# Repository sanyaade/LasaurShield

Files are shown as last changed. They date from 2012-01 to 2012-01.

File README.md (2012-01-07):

The LasaurShield is a custom PCB for the [Lasersaur project](http://lasersaur.com). It's an [Arduino](http://arduino.cc/) [shield](http://arduino.cc/en/Main/ArduinoShields) that connects laser, stepper, stepper driver, stepper power, limit switches, door sensor, water chiller sensor, emergency stop sensor, and Arduino. Starting with v11.10 the core safety functions are also hardwired on the board.

The LasaurShield is designed around the SparkFun Eagle Library, their design and CAM job rules. Check out the [SparkFun Tutorial](http://www.sparkfun.com/tutorials/108) if you are new to this. If you are interesting doing your own production run check out [this tutorial](http://www.sparkfun.com/tutorials/109).

The following Eagle library and design files are being used:

- cam/sparkfun-gerb274x.cam
- dru/LasaurShield.dru
- lbr/[SparkFun.lbr]
- lbr/con-phoenix-254.lbr (comes with Eagle)
- lbr/con-phoenix-508.lbr (comes with Eagle)
- lbr/con-weidmueller-sl35.lbr (comes with Eagle)

**DISCLAIMER:** Please be aware that operating a DIY laser cutter can be dangerous and requires full awareness of the risks involved. You build the machine and you will have to make sure it is safe. The instructions of the Lasersaur project and related software come without any warranty or guarantees whatsoever. All information is provided as-is and without claims to mechanical or electrical fitness, safety, or usefulness. You are fully responsible for doing your own evaluations and making sure your system does not burn, blind, or electrocute people.

Some Notes about Using Eagle
=============================

Eagle is quite powerful but also awkward to use. It's easy to forget how to command the UI.

When designing the schematic
------------------------------
- import parts libraries, Library->Use
- some parts like the NAND gates require you to press the "Invoke" button and place power and ground. Don't ask me why.
- Once the schematic is done, run the electrical checks Tools->Erc

When laying out the board
--------------------------
- load design rules, Tools->Drc  (dru/LasaurShield.dru)
- place components, move/rotate to optimize the ratsnest
- color layers as needed, View->Display/hide layers
  - 121 _tsilk  ... is top silkscreen
  - 122 _bsilk  ... is bottom silkscreen
- run autoroute, 
  - The power of the autorouter is that it can be used incrementally. Some wires can be drawn manually and the autorouter can finish the rest. 
  - Another great approach is to draw some wires roughly (e.g. on one side of the board) then autoroute, rip the manual wires and autoroute again. This way the autorouter follows the general idea but draws the wires nicely.
- if the autorouter should use different trace widths this can be accomplished by defining net classes with different widths, Edit->Net classes
  - air wires of the ratsnest (it actually applies to the entire signal) can then be assigned to the various net classes

When creating the CAM Job (gerber files)
-----------------------------------------
- run final design rule check, Tools->Drc
- Open the CAM Processor, File->Cam Processor
- Open the CAM rule file, File->Open->Job   (cam/sparkfun-gerb274x.cam)
- Press "Process Job"
- At this point Eagle creates a bunch of files in the same directory as the board file. 
  - Top Copper (GTL)
  - Top Soldermask (GTS)
  - Top Silkscreen (GTO)
  - Bottom Copper (GBL)
  - Bottom Soldermask (GBS)
  - Bottom Silkscreen (GBO)
  - Drill File (TXT)
  - Drill Summary (dri)
- before sending these to a manufacturing house check them with [Viewplot](http://www.viewplot.com/) or by uploading a zip to [circuitpeople.com](http://circuitpeople.com/).

Parts List for v11.11 Upgrade
==============================

2   resistor 10 KOhm    271-10K-RC    (making it a total of 7x)
1   e-stop button 24mm    642-A01ES
1   e-stop SPST block    642-A0150B
2   NAND Gates IC    863-MC74AC20NG
1   DIN rail 1m    651-5602100
1   relay 277VAC@25A for DIN rail    528-725BXXSC3ML-24D
8   terminal block for DIN rail    651-3004362
1   terminal block side cover    651-3003020
5   terminal block bridge    651-0201155
1   power supply 24V for DIN rail    845-PS-6024    (replacement)
1   power entry connector, C-20   562-744W-00/04 
1   power entry connector, C-14   161-R30148-E

Test for v11.11
===============

- chiller hard logic ... ok
- limit switches hard logic ... ok

- limit switch input
- chiller input
- overwrite
- rel input

git push -u origin master

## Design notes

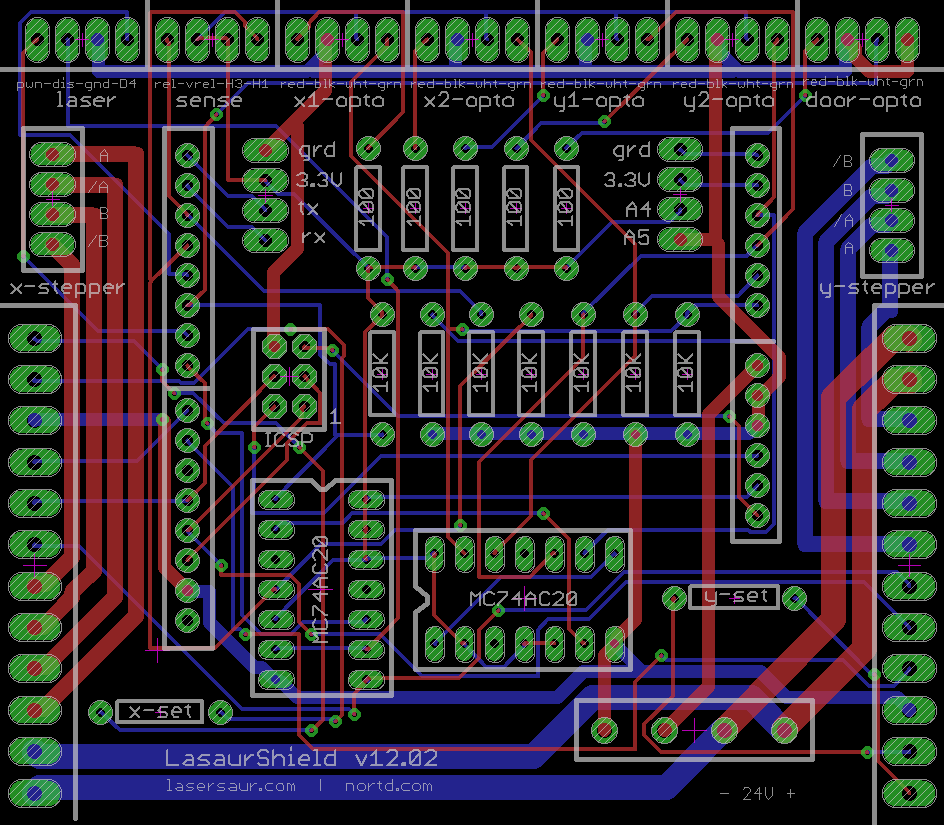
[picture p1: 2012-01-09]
pcb-job-files/LasaurShield.png

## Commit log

2011-10-06 hard logic added for core safety system
    [LasaurShield.brd, LasaurShield.sch]
2011-10-06 power traces optimized, no vias
    [LasaurShield.brd, LasaurShield.sch]
2011-10-06 trace distances fine tuned
    [LasaurShield.brd, LasaurShield.sch]
2011-10-06 checked against sparkfun design rules
    [LasaurShield.brd]
2011-10-06 checked against lasersaur 12mil design rules
    [LasaurShield.brd]
2011-10-06 gerber files generated with sparkfun-gerb274x.cam rules file
    [LasaurShield.brd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]
2011-10-19 first hard logic prototype, all limit switches are ORed to one signal
2011-10-19 second nand IC laid out
    [LasaurShield.brd, LasaurShield.sch]
2011-10-19 gpio terminal added
    [LasaurShield.brd, LasaurShield.sch]
2011-10-20 manual routing done; pre-autorouting
    [LasaurShield.brd, LasaurShield.sch]
2011-10-20 gerber files created
    [LasaurShield.brd, LasaurShield.sch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]
2011-10-20 eagle design process summuriezed
    [LasaurShield.brd]
2011-10-28 bugfix: sad puppy! I had to fix a logical mistake in the way the door switch is connected. It needs to run inverted from the limit switches. On the v11.11 boards this can be hacked quite easily by do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
    [LasaurShield.brd, LasaurShield.sch]
2012-01-09 shields adapted for G203V stepper drivers; slight changes to the silkscreen
    [LasaurShield.brd, LasaurShield.sch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]
